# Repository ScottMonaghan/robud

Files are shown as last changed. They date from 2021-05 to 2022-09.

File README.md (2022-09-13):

# Ro-Bud - Lovable, Accessible, Autonomous Companion
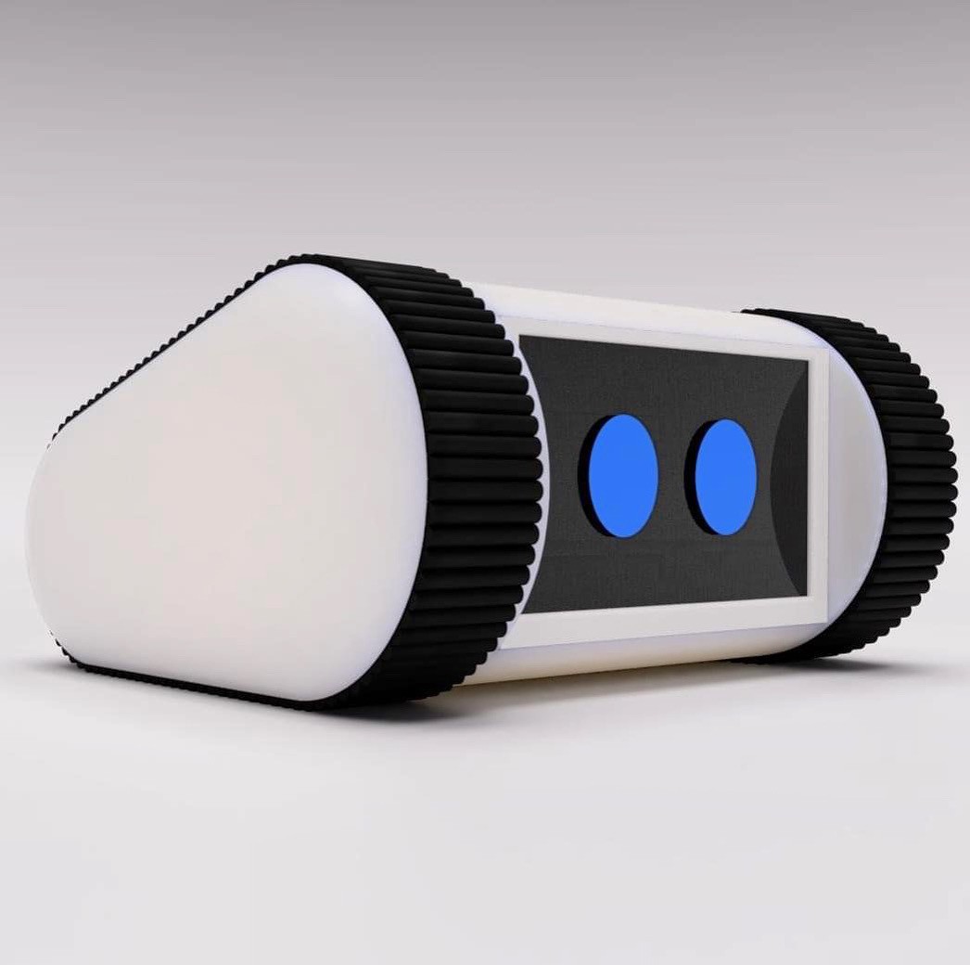
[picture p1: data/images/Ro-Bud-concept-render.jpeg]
Ro-bud
  

## Table of Contents
 * [Summary](#summary)
 * [Description](#description)
 * [Pre-Alpha Build Instructions](#pre-alpha-build-instructions)
   * [Parts Reference](#parts-reference)
   * [Head Assembly](#head-assembly)
 * [Original Project Announcement Videos](#original-project-announcement-videos)
   * [Part 1](#part-1)
   * [Part 2](#part-2)
   * [Part 3](#part-3)
   * [Part 4](#part-4)
## Summary
The Ro-Bud project seeks to create a companion bot that is lovable, accessible to all, and autonomous.  

[Return to Table of Contents](#table-of-contents)

## Description
Challenge: Despite decades of fictional depiction through popular culture, as of 2021, robotic companion bots that even come close to those of popular imagination are not available at scale.

While there have been impressive private for-profit attempts at releasing relatively advanced consumer companion bots, specifically Jibo and Anki Vector, these endeavors ultimately proved commercially unviable, forcing the companies to fold, and effectively removing these wonderfully engineered robots from either availability or full operability (as they were dependent on proprietary services provided by their now-defunct companies).

The Ro-Bud project is an attempt to pick up where Jibo and Ankni left off, and fulfil the dream of providing a consumer robot that is:
1. LOVEABLE - Feels just like a family pet
2. ACCESSIBLE - Can be built by anyone following project instructions with readily available parts with a cost at or under $500
3. AUTONOMOUS - Has it's own goals.  

[Return to Table of Contents](#table-of-contents)

# Alpha Build Instructions
**NOTE: The following build instructions are in-progress and not yet complete**  
Last updated 17-August 2022

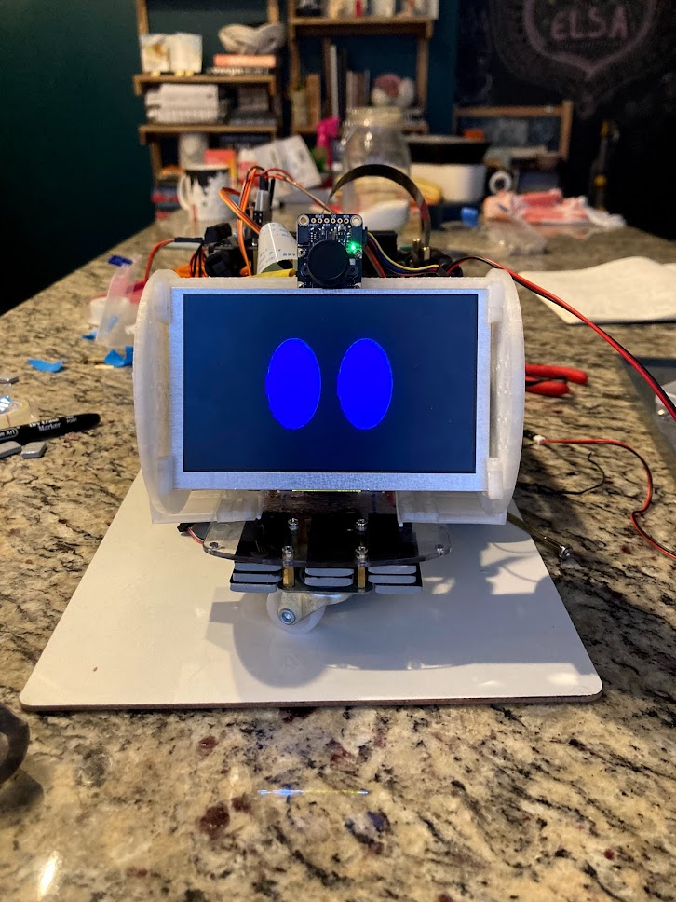
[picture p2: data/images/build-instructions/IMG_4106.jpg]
Pre-Alpha Ro-Bud Build


**Documentation To-Do**
 * [x] Add 3d-printable models
 * [ ] Jetson Wifi Module Install
 * [ ] SD Card Flashing
 * [x] Head Assembly  
 * [ ] Remote VM setup
 * [ ] Remote Operation Instructions

[Return to Table of Contents](#table-of-contents)

## Master Parts Reference
 * A. horizontal braces [stl](./data/stl/robud-horizontal-brace.stl)
 * B. 3-hole fastener [stl](./data/stl/robud-3-hole-fastener.stl)
 * C. 2x8mm round-head self-tapping screws https://www.amazon.com/gp/product/B07NT5288W  
 * D. 2x8mm pan-head-with-washer self-tapping screws https://www.amazon.com/gp/product/B07NTGRFBF  
 * E. BNO055 orientation sensor https://www.adafruit.com/product/4646, https://www.digikey.com/en/products/detail/adafruit-industries-llc/4646/12609996
 * F. SainSmart IMX219 Camera Module https://www.amazon.com/gp/product/B07VFFRX4C  
 * G. VL53L0X time-of-flight distance sensor https://www.adafruit.com/product/3317  
 * H. 1-hole 2mm screw fastener [stl](./data/stl/robud-1-hole-fastener.stl)
 * I. 300mm 15-pin camera ribbon cable https://www.adafruit.com/product/1648
 * J. 100mm Stemma QT JST SH 4-pin cable https://www.adafruit.com/product/4210
 * K. display fastener [stl](./data/stl/robud-display-fastener.stl)
 * L. servo adapter [stl](./data/stl/robud-servo-adapter.stl)
 * M. head barrel wall [stl](./data/stl/robud-head-barrel-wall.stl)
 * N. head shaft adapter [stl](./data/stl/robud-head-shaft-adapter.stl)
 * O. bearing https://www.amazon.com/gp/product/B07S1B3MS6  
 * Q. MG90S 9G micro servo https://www.amazon.com/gp/product/B07F7VJQL5  
 * R. ~~5in display https://www.adafruit.com/product/1678, https://www.digikey.com/en/products/detail/adafruit-industries-llc/1678/10670051
 * S. ~~40 Pin Flexible Flat Ribbon Cable 0.5mm Pitch - 200mm https://www.amazon.com/gp/product/B07C4P6S43
 * T. mono enclosed speaker - 3W 4 Ohm https://www.adafruit.com/product/3351  
 * U. head L bracket [stl](./data/stl/robud-head-L-bracket.stl)
 * V. servo horn (included with servo(Q))
 * W. servo screw (included with servo(Q))
 * CC. SparkFun Qwiic SHIM for Raspberry Pi https://www.sparkfun.com/products/15794
 * DD. Stacking Header for Pi A+/B+/Pi 2/Pi 3 - 2x20 Extra Tall Header https://www.adafruit.com/product/1979
 * EE. Adafruit DC & Stepper Motor Bonnet for Raspberry Pi https://www.adafruit.com/product/4280
 * FF. Break-away 0.1" male header https://www.adafruit.com/product/392
 * GG. Male/Male Jumper Wires - 20 x 6" (150mm) https://www.adafruit.com/product/1957
 * HH. Female/Female Jumper Wires - 20 x 6" (150mm)Female/Female Jumper Wires - 20 x 6" (150mm)
 * II. Heat shrink tubing https://www.adafruit.com/product/1649
 * JJ. 3.5mm (1/8") Stereo Audio Plug Terminal Block https://www.adafruit.com/product/2790
 * KK. Rocker toggle switch (comes with chassis kit)
 * LL. Servo Tester https://www.amazon.com/gp/product/B07TQSKLBK
 * MM. PCA9685 16 Channel 12 Bit PWM Servo Driver https://www.amazon.com/gp/product/B07RMTN4NZ
 * NN. Baseus Power Bank, 65W 20000mAh Laptop Portable Charger https://www.amazon.com/gp/product/B08THCNNCS
 * OO. x2 USB-A Male Plug to 5-pin Terminal Block https://www.amazon.com/gp/product/B07H53X194 (2-pack), https://www.digikey.com/en/products/detail/adafruit-industries-llc/3628/7931507 (1-pack)
 * PP. x2 Stacking Header for Pi https://www.adafruit.com/product/1979, https://www.digikey.com/en/products/detail/adafruit-industries-llc/1979/6238003, https://www.amazon.com/gp/product/B071XCHZNB/(4 pack)
 * QQ. M2.5 brass stand-off kit https://www.amazon.com/gp/product/B075K3QBMX/ (or equivalent)
 * RR. 22AWG Silicone Hook Up Wire (stranded) https://www.amazon.com/gp/product/B07T4SYVYG/ (or equivalent, you want not-too-stiff wire than can handle 4 amps)
 * SS. STEMMA QT / Qwiic JST SH 4-Pin Cable - 400mm long https://www.adafruit.com/product/5385, https://www.digikey.com/en/products/detail/adafruit-industries-llc/5385/16546436
 * TT. Heat Shrink Tubing https://www.amazon.com/gp/product/B01MFA3OFA (can be subbed with electrical tape, or equivalent)
 * UU. 5.0" 40-pin 800x480 TFT Display without Touchscreen https://www.adafruit.com/product/1680
 * VV. TFP401 HDMI/DVI Decoder to 40-Pin TTL Breakout - Without Touch https://www.adafruit.com/product/2218
 * WW. 40-pin FPC Extension Board + 200mm Cable https://www.adafruit.com/product/2098

[Return to Table of Contents](#table-of-contents)
 
## Head Assembly
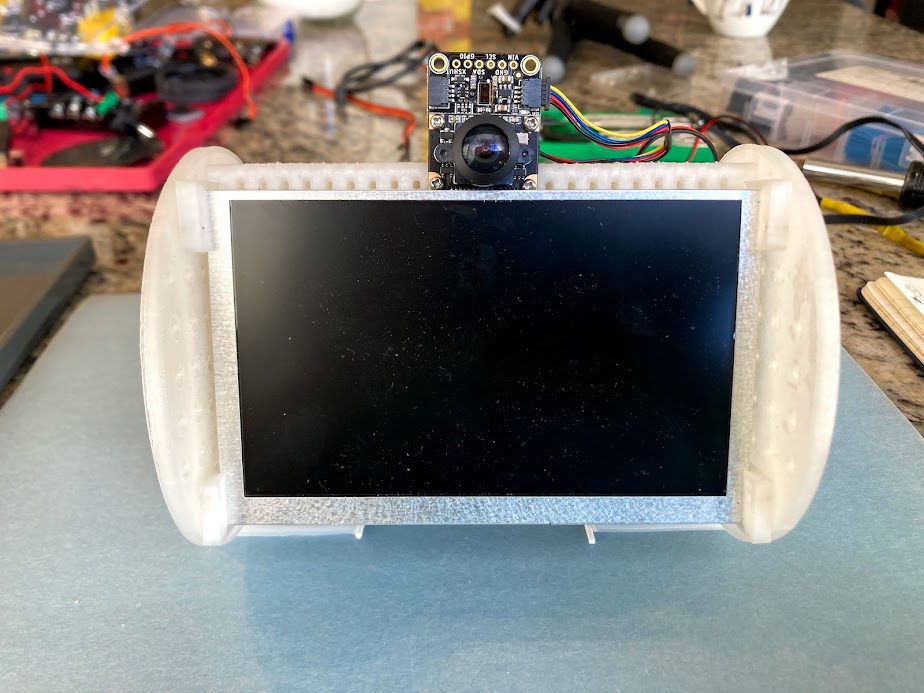
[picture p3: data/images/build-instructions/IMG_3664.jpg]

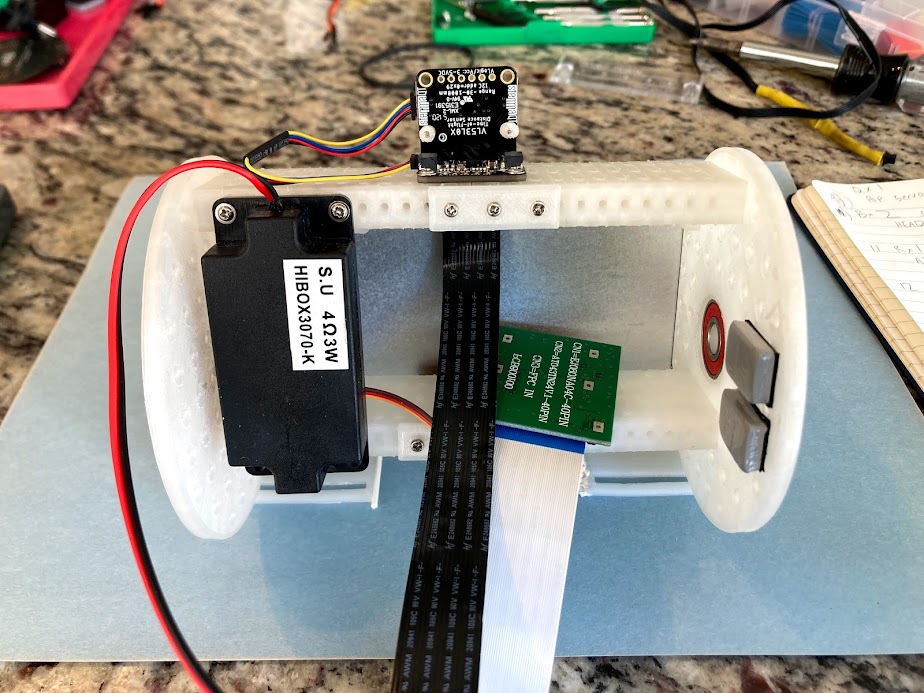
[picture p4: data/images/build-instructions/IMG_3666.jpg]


**Full list of Head Assembly Parts**
   * 3d Printed Parts (Ender 3 settings - PLA, Raft recommended, defaults otherwise) 
     * x4 A. horizontal braces [stl](./data/stl/robud-horizontal-brace.stl)
     * x3 B. 3-hole fastener  [stl](./data/stl/robud-3-hole-fastener.stl)
     * x2 H. 1-hole 2mm screw fastener [stl](./data/stl/robud-1-hole-fastener.stl)
     * x4 K. display fastener [stl](./data/stl/robud-display-fastener.stl)
     * x1 L. servo adapter [stl](./data/stl/robud-servo-adapter.stl)
     * x2 M. head barrel wall [stl](./data/stl/robud-head-barrel-wall.stl)
     * x1 N. head shaft adapter [stl](./data/stl/robud-head-shaft-adapter.stl)
     * x2 U. head L bracket [stl](./data/stl/robud-head-L-bracket.stl)

   * Adafruit (recommend sourcing from DigiKey for best US price/shipping)
     * x1 E. BNO055 orientation sensor https://www.adafruit.com/product/4646, https://www.digikey.com/en/products/detail/adafruit-industries-llc/4646/12609996 (often out of stock due to chip shortage. Check DigiKey, Adafruit, Mouser & Amazon)
     * x1 G. VL53L0X time-of-flight distance sensor https://www.adafruit.com/product/3317, https://www.digikey.com/en/products/detail/adafruit-industries-llc/3317/6569762
     * x1 I. 300mm 15-pin camera ribbon cable https://www.adafruit.com/product/1648, https://www.digikey.com/en/products/detail/adafruit-industries-llc/1648/7035020
     * x1 J. 100mm Stemma QT JST SH 4-pin cable https://www.adafruit.com/product/4210, https://www.digikey.com/en/products/detail/adafruit-industries-llc/4210/10230021
     * ~~x1 R. 5in display https://www.adafruit.com/product/1678
     * x1 T. mono enclosed speaker - 3W 4 Ohm https://www.adafruit.com/product/3351  

   * Amazon
     * x7 C. 2x8mm round-head self-tapping screws https://www.amazon.com/gp/product/B07NT5288W  
     * x20 D. 2x8mm pan-head-with-washer self-tapping screws https://www.amazon.com/gp/product/B07NTGRFBF 
     * x1 F. SainSmart IMX219 Camera Module https://www.amazon.com/gp/product/B07VFFRX4C  
     * x1 O. bearing https://www.amazon.com/gp/product/B07S1B3MS6 
     * x1 Q. MG90S 9G micro servo https://www.amazon.com/gp/product/B07F7VJQL5
     * x1 ~~S. 40 Pin Flexible Flat Ribbon Cable 0.5mm Pitch - 200mm https://www.amazon.com/gp/product/B07C4P6S43
     * x1 V. servo horn (packaged with Q MG90S 9G micro servo)
     * x1 W. server screw (packaged with Q MG90S 9G micro servo)
     * x1 LL. Servo Tester https://www.amazon.com/gp/product/B07TQSKLBK
     * x1 MM. PCA9685 16 Channel 12 Bit PWM Servo Driver https://www.amazon.com/gp/product/B07RMTN4NZ
     * x1 UU. 5.0" 40-pin 800x480 TFT Display without Touchscreen https://www.adafruit.com/product/1680
     * x1 VV. TFP401 HDMI/DVI Decoder to 40-Pin TTL Breakout - Without Touch https://www.adafruit.com/product/2218
     * x1 WW. 40-pin FPC Extension Board + 200mm Cable https://www.adafruit.com/product/2098
   
### 1. Attach two horizontal braces(A) with 3-hole fastener(B) & attach BNO-055  orientation sensor(E)  

**Parts:**  
   * x2 A. horizontal braces  
   * x1 B. 3-hole fastener  
   * x3 C. 2x8mm round-head self-tapping screws  
   * x4 D. 2x8mm pan-head-with-washer self-tapping screws  
   * x1 E. BNO055 orientation sensor

>_**Notes:**_ 
>   * _Make sure Y axis of BNO055(E) points toward picture as shown in image_
>   * _Only fasten one side of the horizontal braces(E)_
     
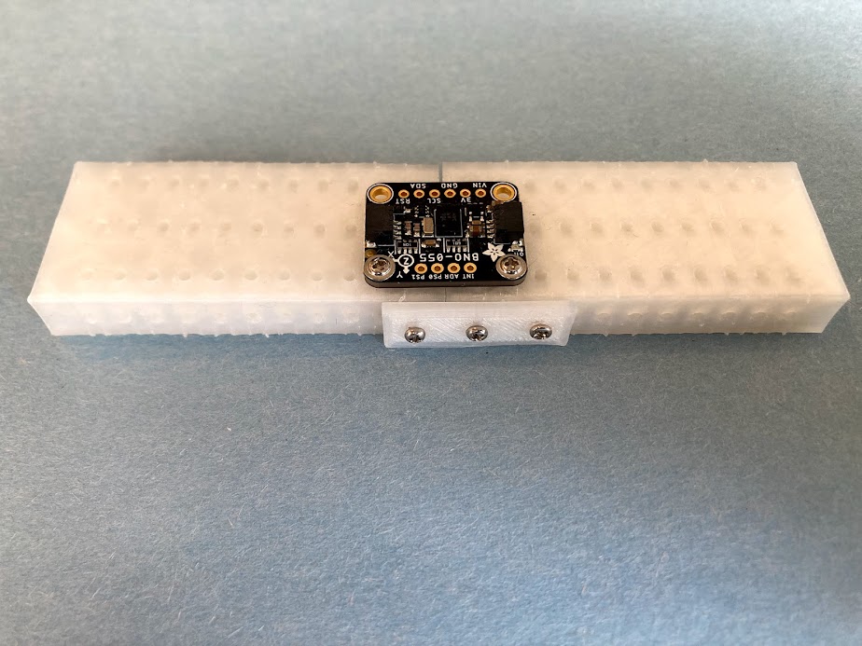
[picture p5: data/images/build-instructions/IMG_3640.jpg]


---
### 2. Turn 180 degrees and attach camera(F) 

**Parts:**  
   * x1 F. SainSmart IMX219 Camera Module
   * x2 C. 2x8mm round-head self-tapping screws

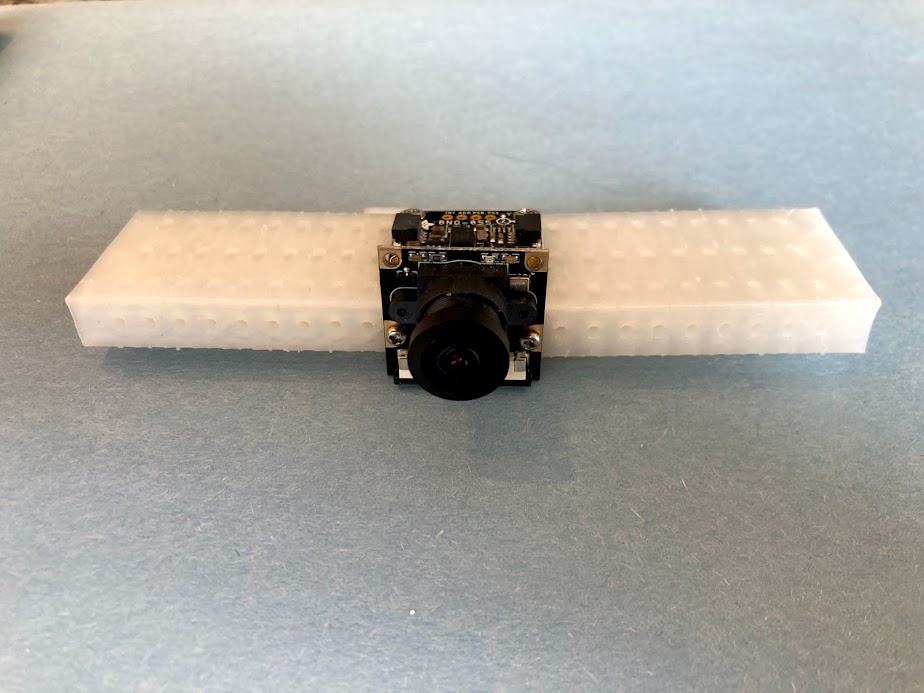
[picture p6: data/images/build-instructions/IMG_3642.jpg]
Head Assembly Step 2


---    
### 3. Attach VL53L0X time-of-flight distance sensor(G) 

**Parts:** 
  * x2 H. 1-hole 2mm screw fastener  
  * x2 C. 2x8mm round-head self-tapping screws  
  * x1 G. VL53L0X time-of-flight distance sensor  
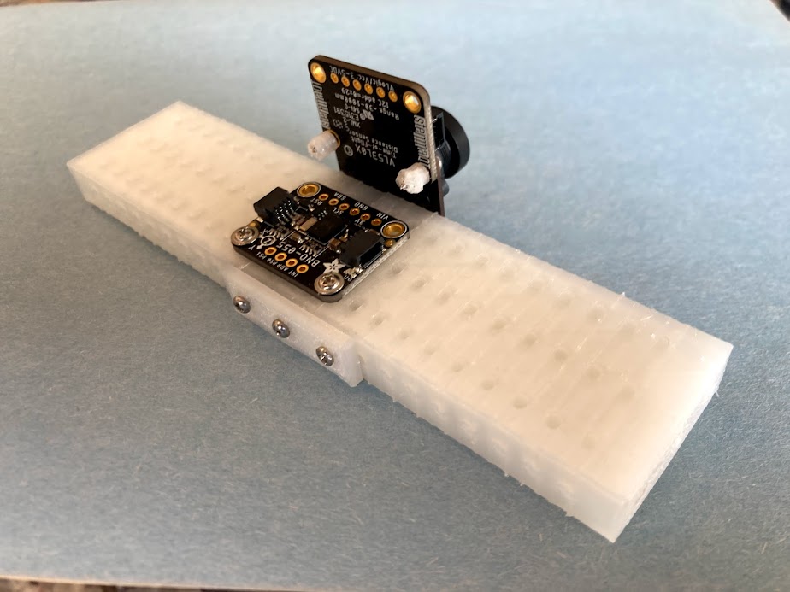
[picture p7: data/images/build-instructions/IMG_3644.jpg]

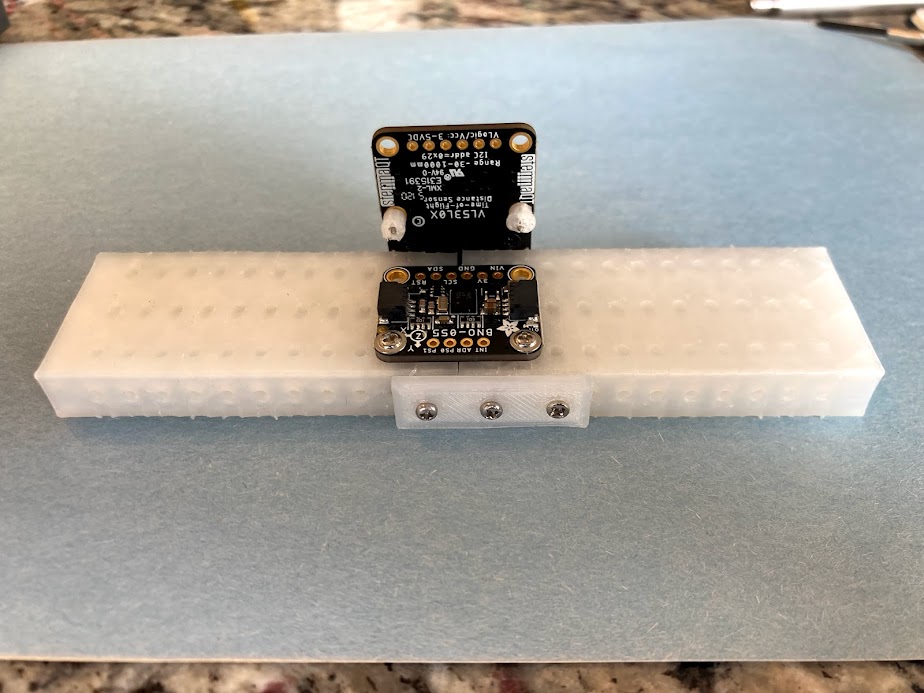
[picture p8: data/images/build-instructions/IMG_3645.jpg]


---     
### 4. Attach camera 15-pin ribbon(I) cable & STEMMA QT cable(J)

**Parts:** 
  * x1 I. 300mm 15-pin camera ribbon cable
  * x1 J. 100mm Stemma QT JST SH 4-pin cable

>_**Notes:**_ 
>   * _Make sure pins of ribbon cable are facing toward contacts and fastened securely_
>   * _Attatch STEMMA QT cable(J) securely to right STEMMA sockets on VL53L0X(G) and BNO055(E)_
   
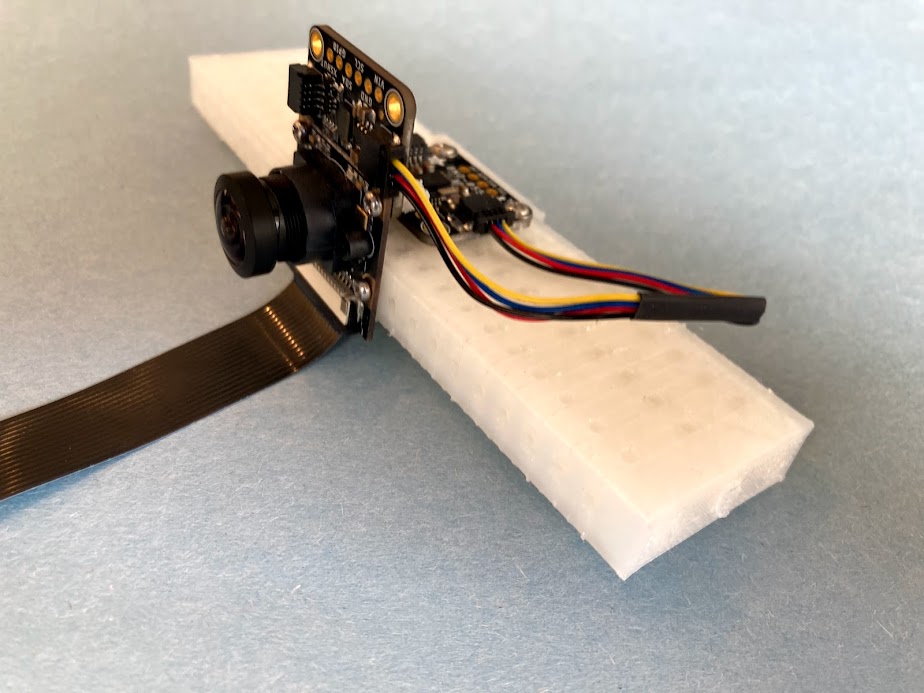
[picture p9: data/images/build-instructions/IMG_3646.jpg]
Head Assembly Step 4


---   
### 5. Attach display fasteners(K) and servo adapter(L) to left barrel wall(M)
**Parts:**  
 * x1 M. head barrel wall
 * x1 L. servo adapter
 * x2 K. display fastener
 * x4 D. 2x8mm pan-head-with-washer self-tapping screws

>_**Notes:**_
>   * _Make sure fasteners and raised center lip are on opposite sides_
>   * _Make sure slotted sides of the display fasteners(K) are face up, with open sides pointed inside the circle, and closed ends are pointed out_
>   * _Make sure servo adapter is oriented as shown in image_
>   * _If servo adapter cannot be popped in, soften with a hair dryer or heat gun_
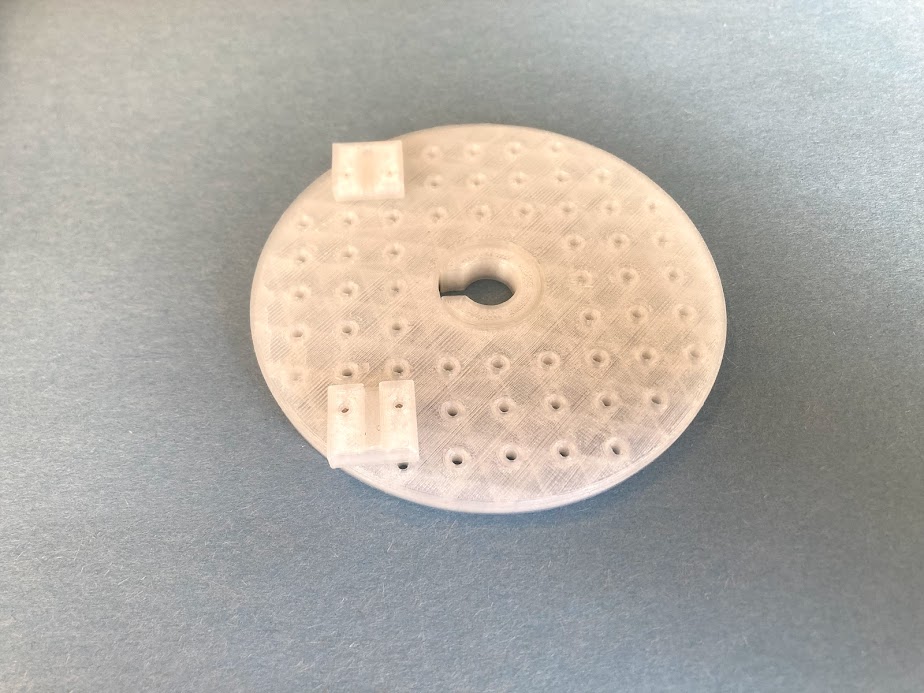
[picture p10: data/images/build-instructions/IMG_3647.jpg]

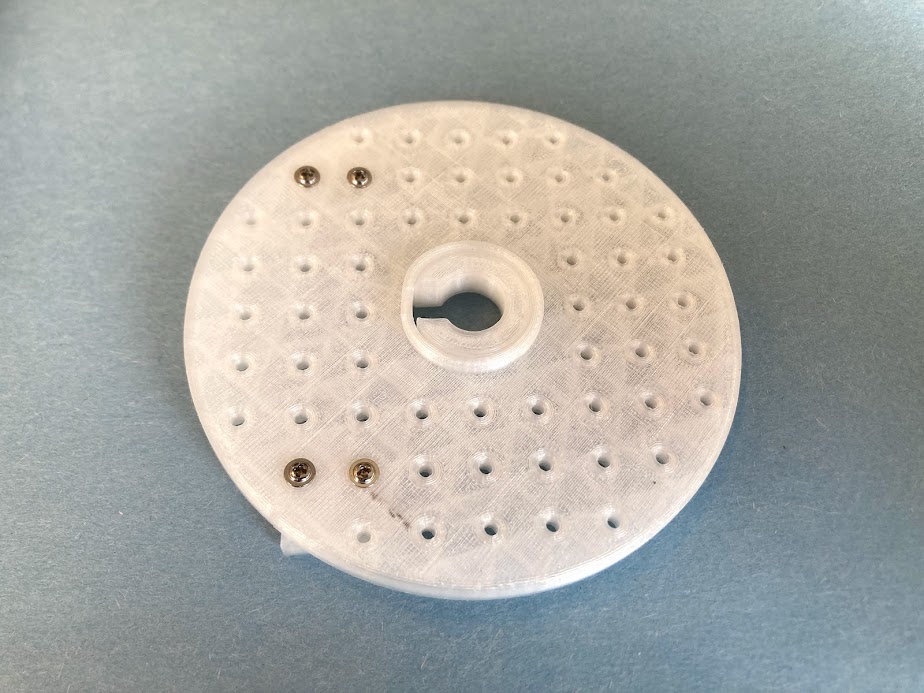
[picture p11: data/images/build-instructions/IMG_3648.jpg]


---   
### 6. Use the servo tester to set servo to neutral position (90 degrees)
**Parts:**  
   * x1 Q. MG90S 9G micro servo
   * x1 LL. Servo Tester
---   
### 7. Pop servo(Q) into left barrel wall(M)
**Parts:**  
   * x1 Q. MG90S 9G micro servo  
   * x2 M. left barrel wall(M) from step 5  

>_**Notes:**_
>   * _Body of servo should be on same side as fasteners from step 5_  
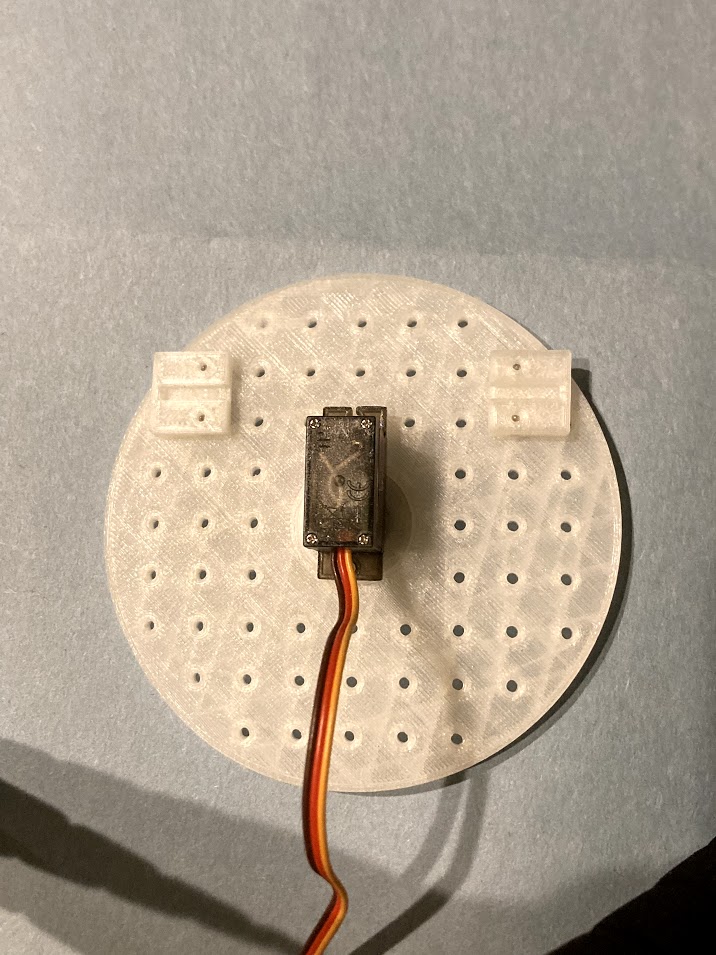
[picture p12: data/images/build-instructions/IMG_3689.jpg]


---   
### 8. Add shaft(N) to bearing(O)
**Parts:**  
 * x1 N. head shaft adapter 
 * x1 O. bearing 

>_**Notes:**_
>   * _If shaft cannot be popped in, soften with a hair dryer or heat gun_
>   * _The longer side of the shaft should be in the bearing_
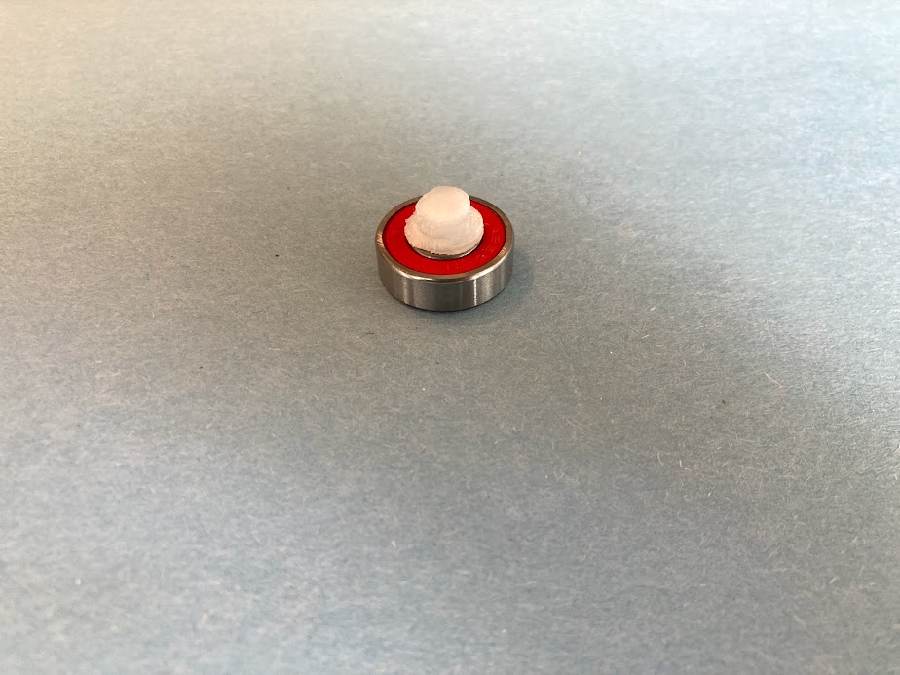
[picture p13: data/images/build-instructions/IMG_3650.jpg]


---   
### 9. Attach display fasteners(K) to right barrel wall(M)
**Parts:**  
 * x1 M. head barrel wall
 * x2 K. display fastener

>_**Notes:**_
>  * _Make sure fasteners and raised center lip are on opposite sides_
>  *_Balance weights shown in photo are no-longer used. Please ignore_
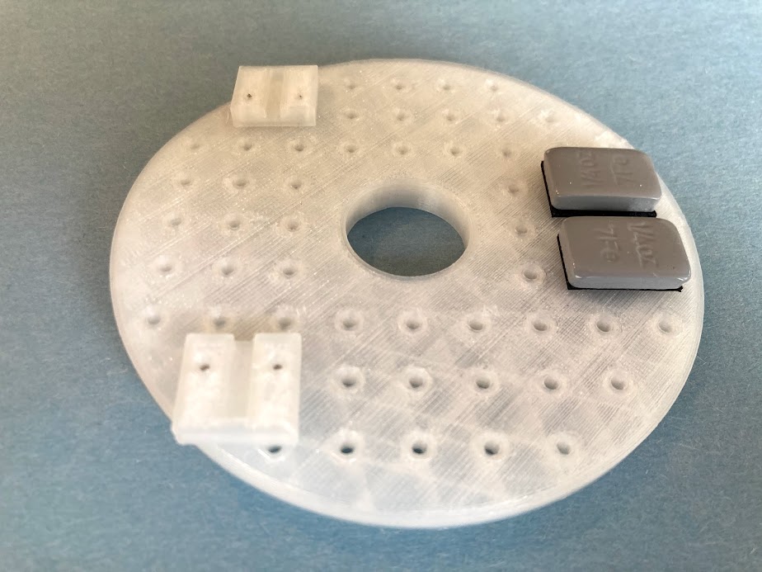
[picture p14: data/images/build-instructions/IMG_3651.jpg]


---   
### 10. Pop bearing(O) into right barrel wall(M)
**Parts:**  
 * x1 bearing(O) with shaft(N) from step 8
 * x1 right barrel wall(M) from step 9

>_**Notes:**_
>   * _Make sure shaft is on the opposite side of the clips & weights_
>   * _If bearing cannot be popped in, soften with a hair dryer or heat gun_
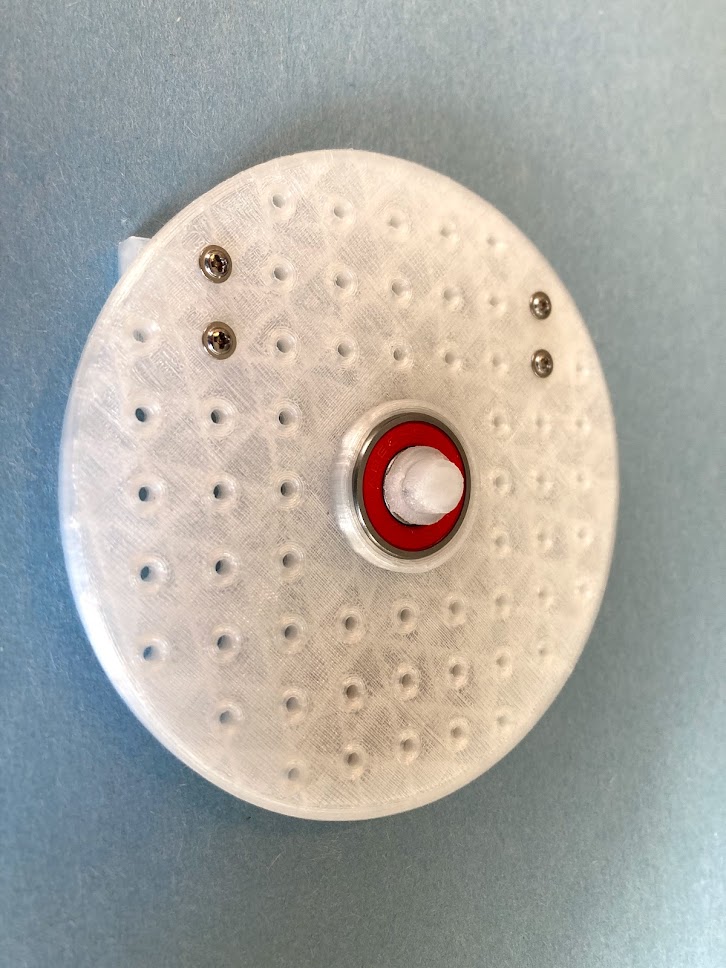
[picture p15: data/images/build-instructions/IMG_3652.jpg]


---   
### 11. Attach two horizontal braces(A) with two 3-hole fasteners(B) to create lower head brace
**Parts:**  
   * x2 A. horizontal braces  
   * x2 B. 3-hole fasteners  

>_**Notes:**_
>  * _Make sure to add 3-hole fastener(B) to both sides_
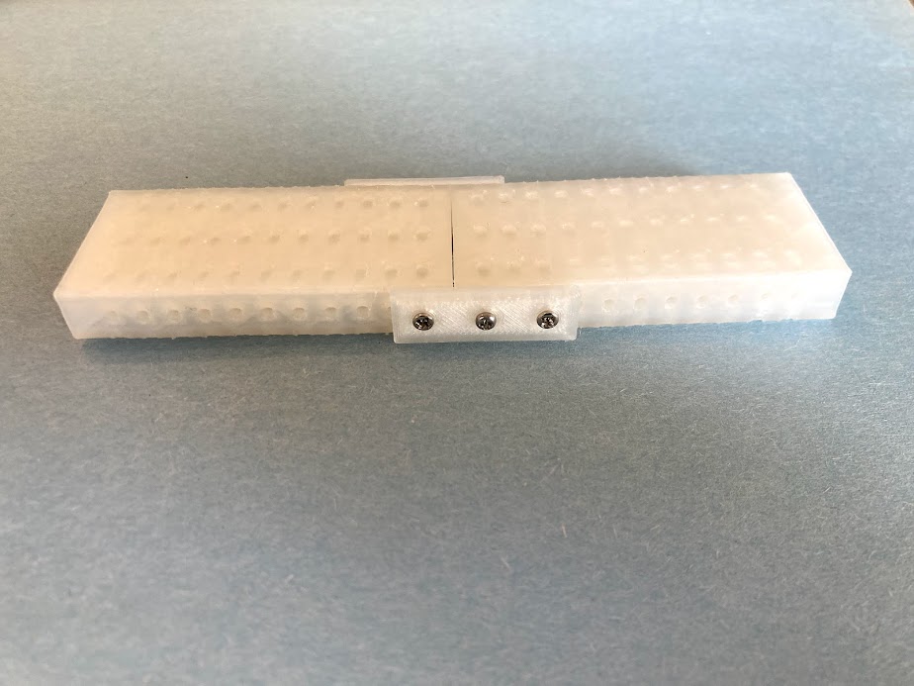
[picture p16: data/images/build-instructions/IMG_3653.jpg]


---   
### 12. Attach bottom head brace to left barrel wall
**Parts:**  
   * x1 Left barrel wall with servo (from step 7)  
   * x1 Lower horizontal head brace (from step 11)  
   * x2 D. 2x8mm pan-head-with-washer self-tapping screws
  
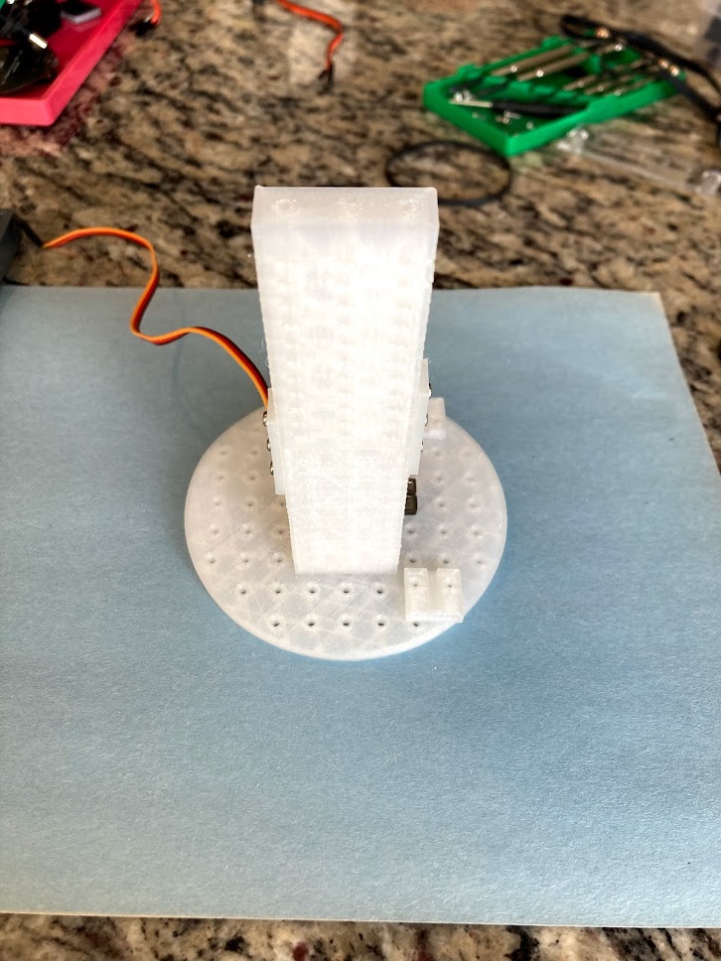
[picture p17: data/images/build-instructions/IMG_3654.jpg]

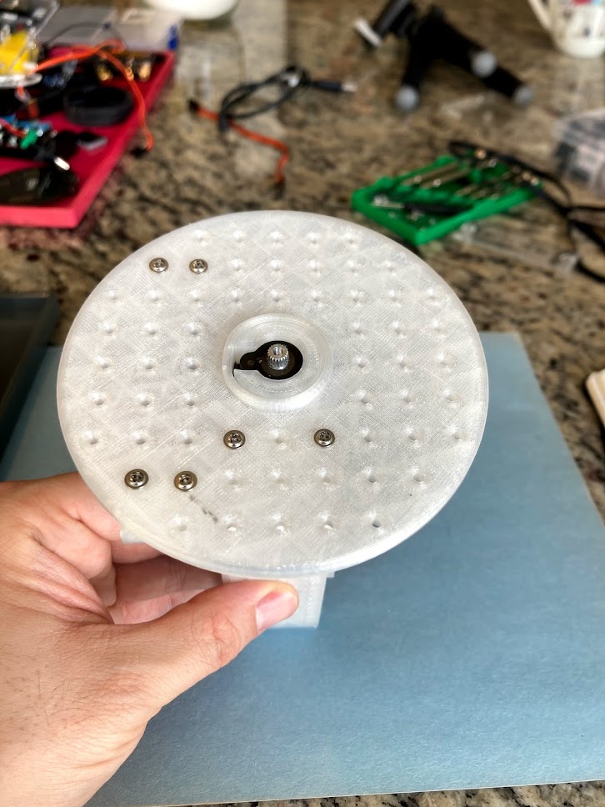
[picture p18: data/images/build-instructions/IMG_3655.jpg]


---   
### 13. Attach top head brace to left barrel wall
**Parts:**  
   * x1 Left barrel wall with servo (from step 12)  
   * x1 Top horizontal head brace with camera (from step 1)  
   * x2 D. 2x8mm pan-head-with-washer self-tapping screws
  
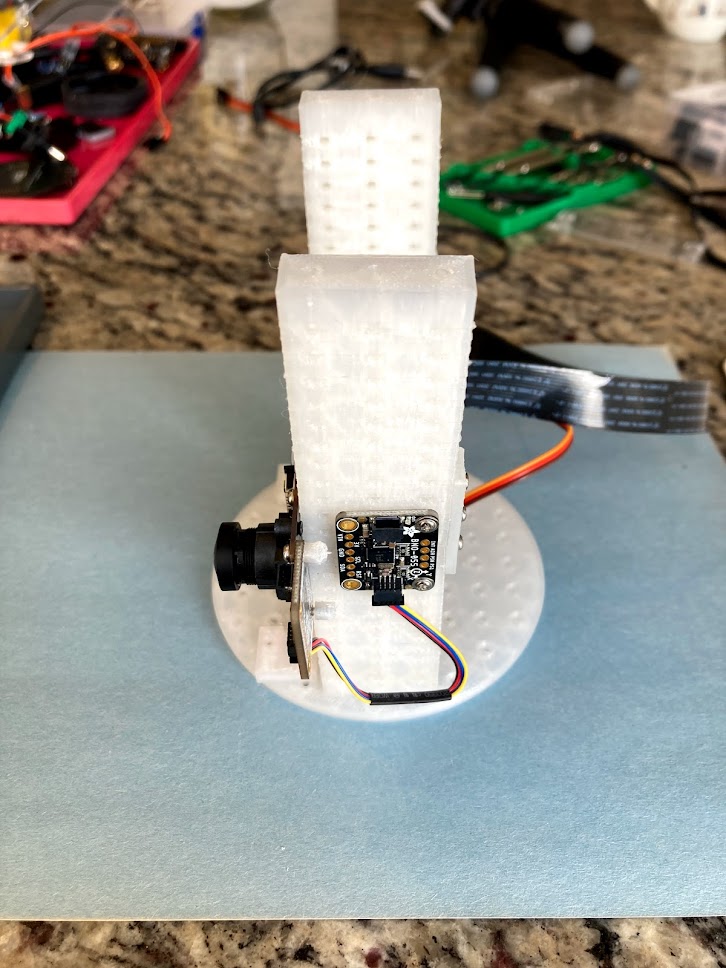
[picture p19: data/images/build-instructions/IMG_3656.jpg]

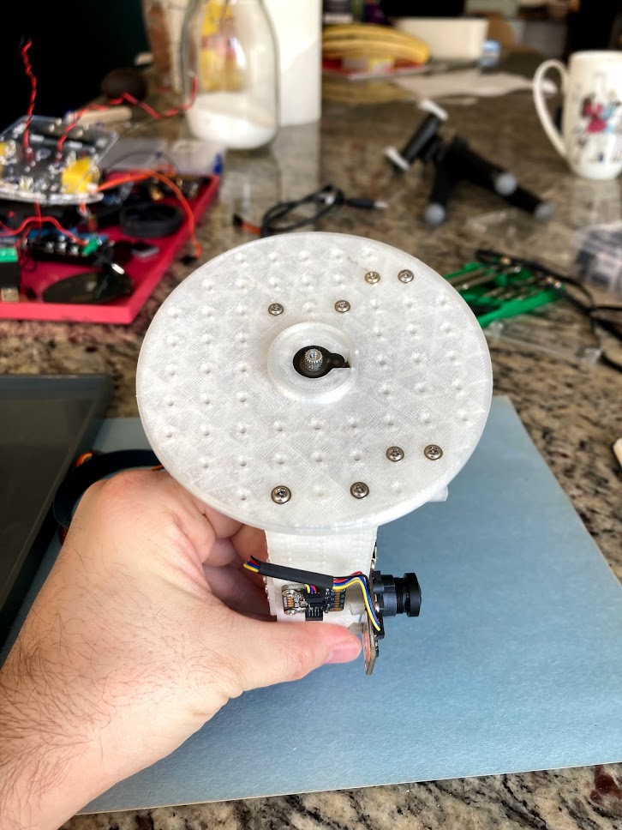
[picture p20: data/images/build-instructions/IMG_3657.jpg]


---   
### 14. Attach 40-pin display ribbon(S) to display(R)  
**Parts:**  
   * x1 R. 7in display  
   * x1 S. 250mm 40pin display ribbon cable  

>_**Notes:**_
>   * _Make sure pins of ribbon cable are facing toward contacts and fastened securely_
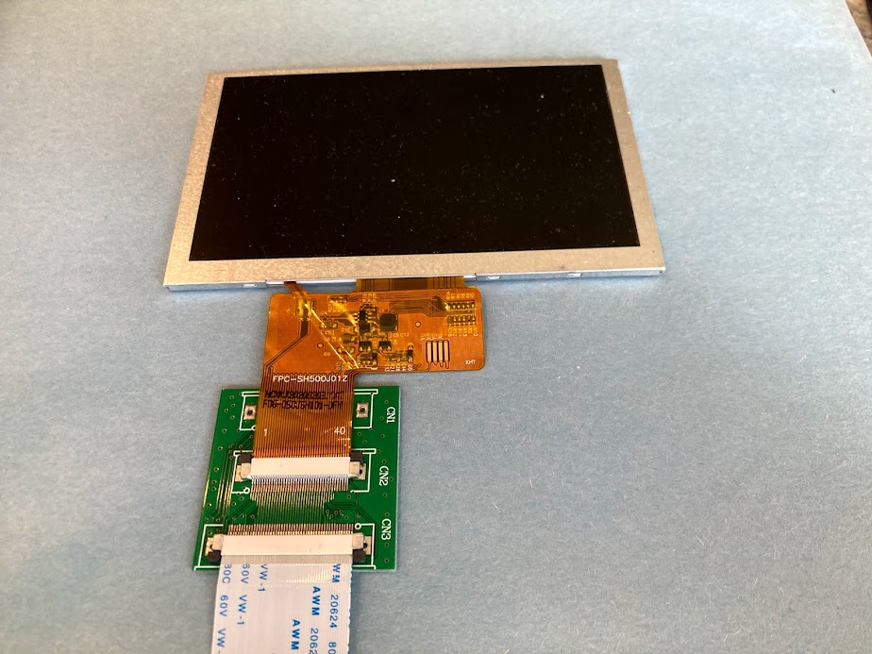
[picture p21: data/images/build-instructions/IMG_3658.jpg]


---   
### 15. Pop display(S) into clips of left barrel wall(M)
**Parts:**  
   * x1 R. 7in display  
   * x1 left barrel wall with servo (from step 12)  

>_**Notes:**_
>   * _Make sure the cables are on the bottom (opposite camera) and feed bewtween both horizontal braces_

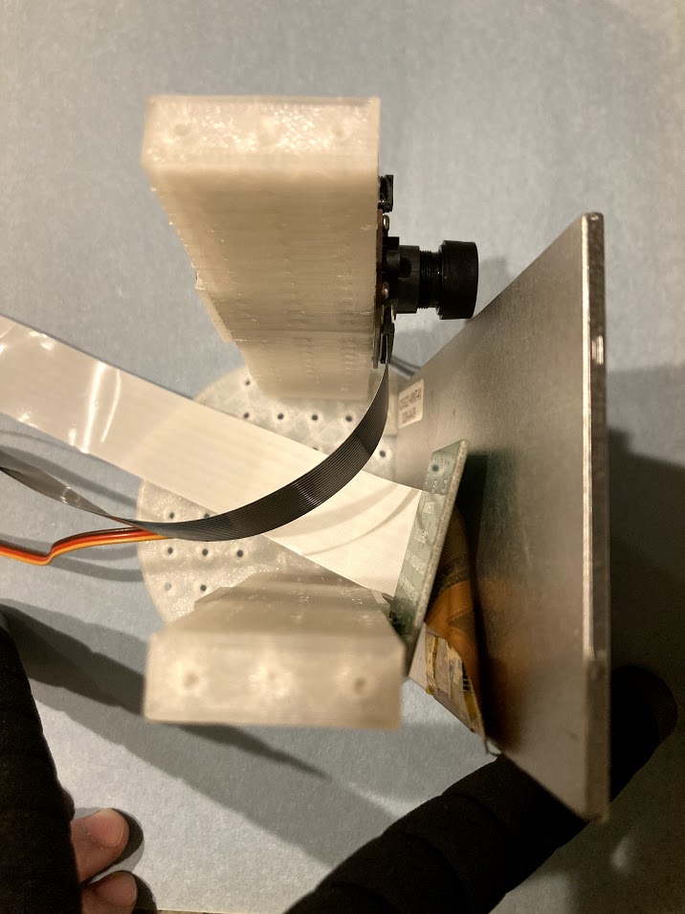
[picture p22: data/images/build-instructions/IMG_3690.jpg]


---   
### 16. Pop right barrel(M) display fasteners(K) onto display and secure to horizontal braces(A) 
**Parts:**  
   * x1 right barrel wall(M) with bearing and shaft (from step 10)
   * x2 D. 2x8mm pan-head-with-washer self-tapping screws

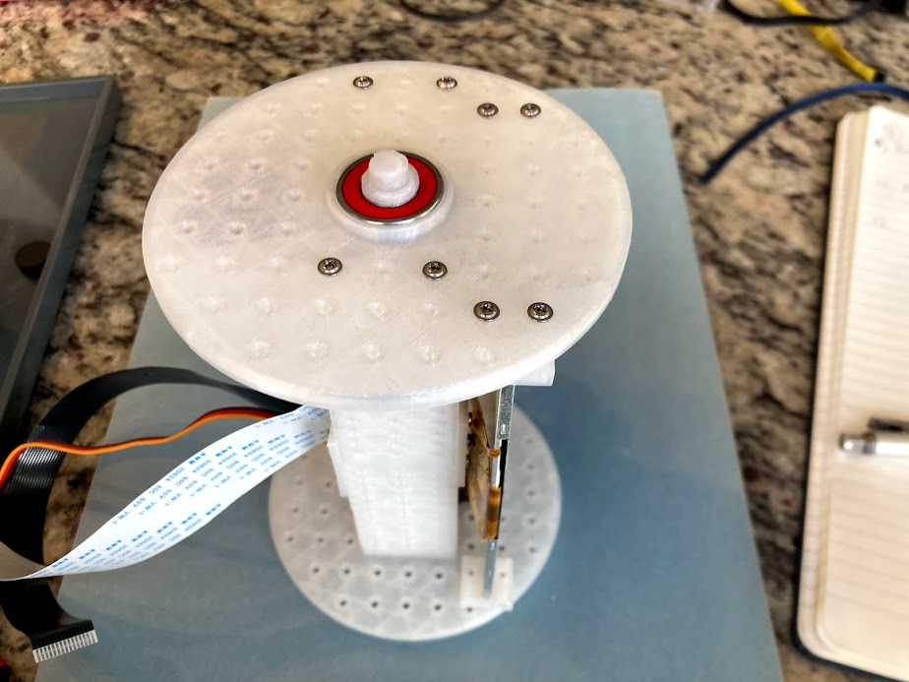
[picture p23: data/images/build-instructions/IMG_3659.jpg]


---   
### 17. Attach speaker(T)
**Parts:**  
   * x1 T. mono enclosed speaker - 3W 4 ohm
   * x2 D. 2x8mm pan-head-with-washer self-tapping screws

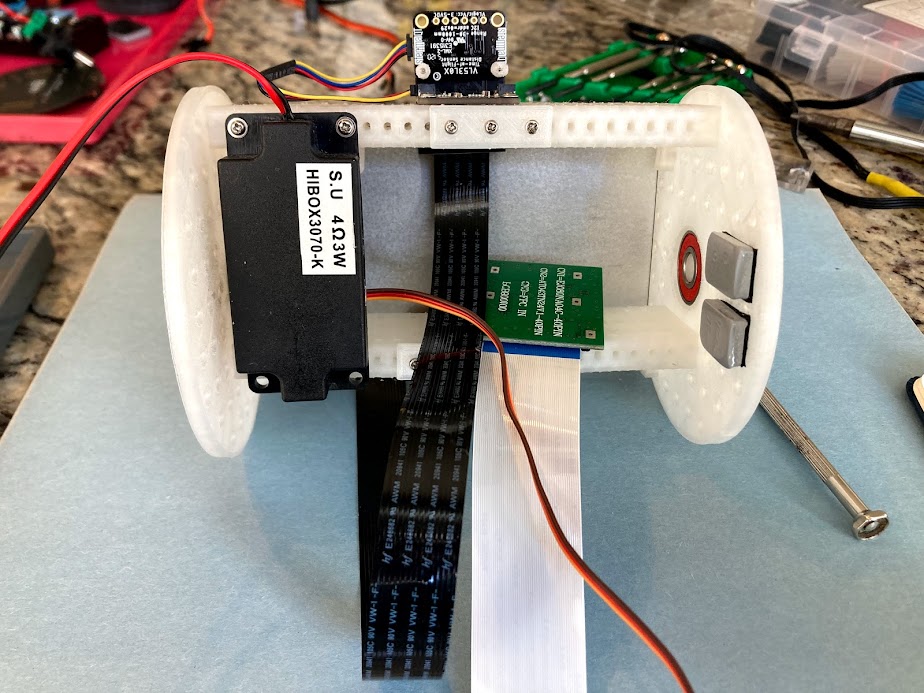
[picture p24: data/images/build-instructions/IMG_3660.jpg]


---   
### 18. Pop right L bracket(U) on bearing shaft
**Parts:**  
   * x1 U. head L bracket

>_**Notes:**_
>   * _If shaft does not pop onto L bracket, use hair dryer or heat gun to soften_

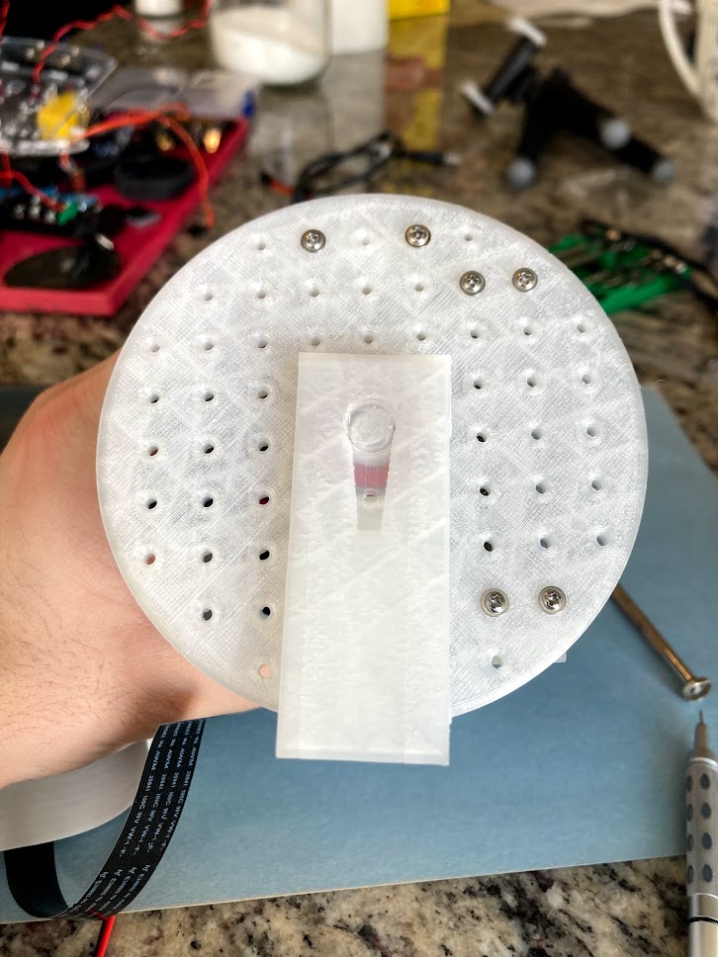
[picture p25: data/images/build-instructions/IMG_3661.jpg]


---   
### 19. Attatch servo horn to remaining L bracket(L) and secure with screw(D)
**Parts:**  
   * x1 U. head L bracket
   * x1 V. servo horn
   * x1 D. 2x8mm pan-head-with-washer self-tapping screw

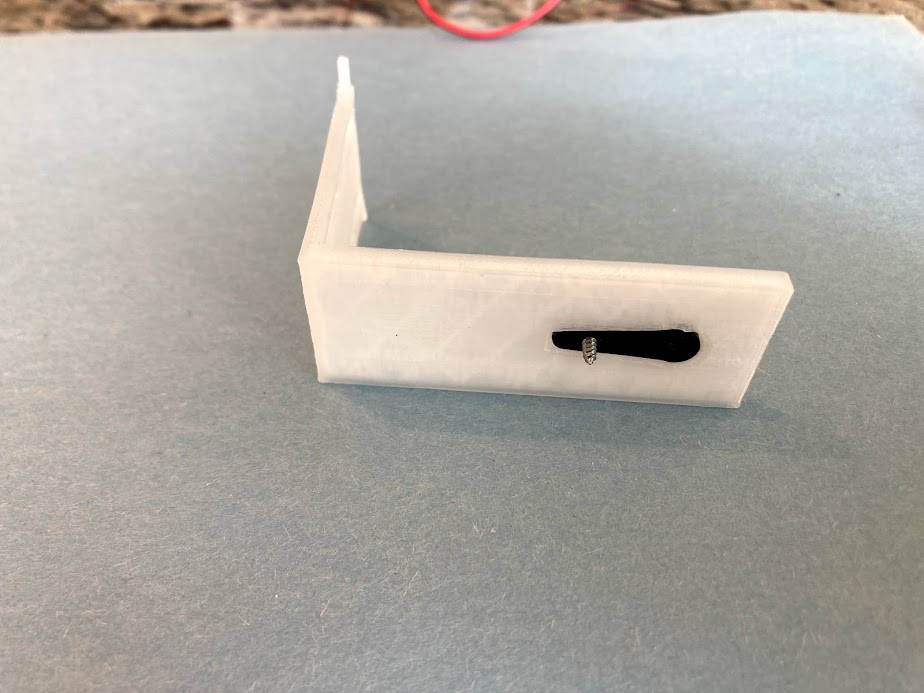
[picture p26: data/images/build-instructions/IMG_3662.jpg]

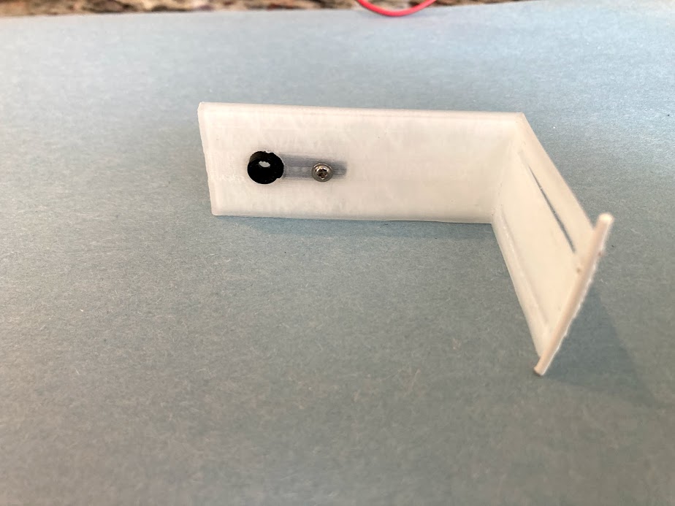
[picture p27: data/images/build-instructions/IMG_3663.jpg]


---   
### 20. Secure left L bracket to head with servo screw(W)
**Parts:**  
   * x1 W. server screw

>_**Notes:**_
>  * _IMPORTANT: The servo horn should be pointing straight down attached with screen pointing straight left_
>  * _Be careful not to turn servo shaft when attaching. If you do, repeat step 6._

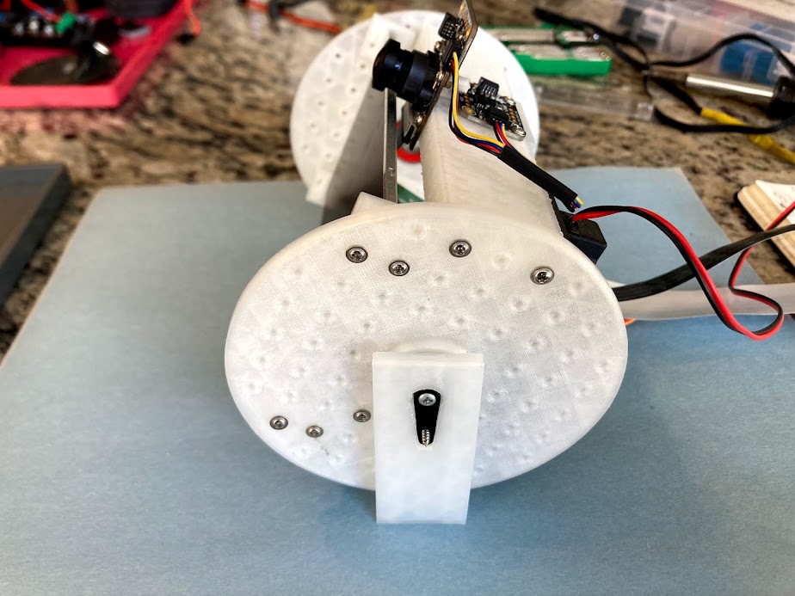
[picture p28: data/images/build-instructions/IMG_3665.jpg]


---   
### 21. The head is now complete and should match the images below:  

Head Assembly Step 5
Head Assembly Step 5
Head Assembly Step 5
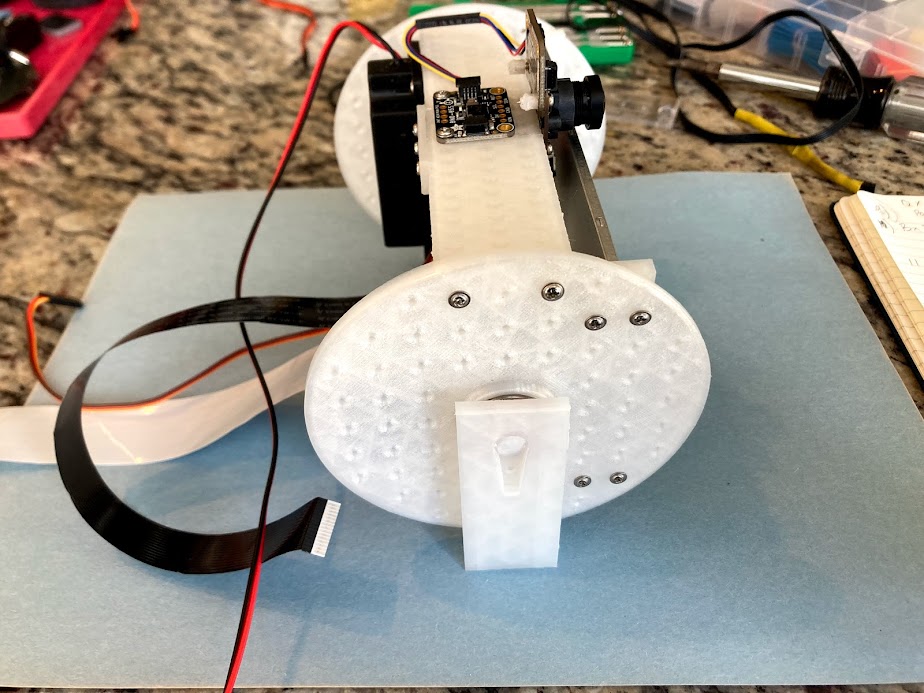
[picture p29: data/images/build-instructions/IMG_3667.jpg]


[Return to Table of Contents](#table-of-contents)

---
## Original Project Announcement Videos  
These videos are the original annoucement and project plan for Ro-Bud uploaded to TikTok on 17-April 2021.  

[Return to Table of Contents](#table-of-contents)
### Part 1  
Ro-Bud Project - Part 1 (https://www.youtube.com/watch?v=bj4LzYycwYc)  

[Return to Table of Contents](#table-of-contents)
### Part 2
Ro-Bud Project - Part 2 (https://www.youtube.com/watch?v=H4fC_qm8pPo)  

[Return to Table of Contents](#table-of-contents)
### Part 3
Ro-Bud Project - Part 3 (https://www.youtube.com/watch?v=r7C16MHGqBg)  

[Return to Table of Contents](#table-of-contents)
### Part 4
Ro-Bud Project - Part 4 (https://www.youtube.com/watch?v=n2G9MuK9-XE)  

[Return to Table of Contents](#table-of-contents)

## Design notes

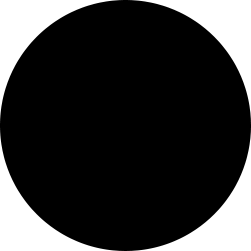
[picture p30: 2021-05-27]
robud_face/Images/robud_round_lid.png

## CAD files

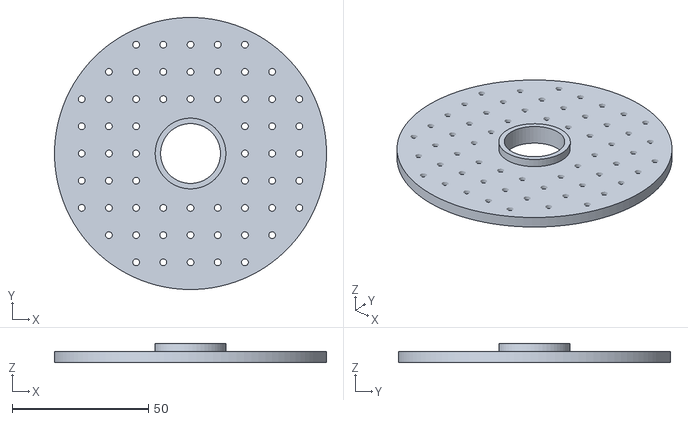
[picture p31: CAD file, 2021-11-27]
data/stl/robud-head-barrel-wall.stl
100.0 x 100.0 x 7.00

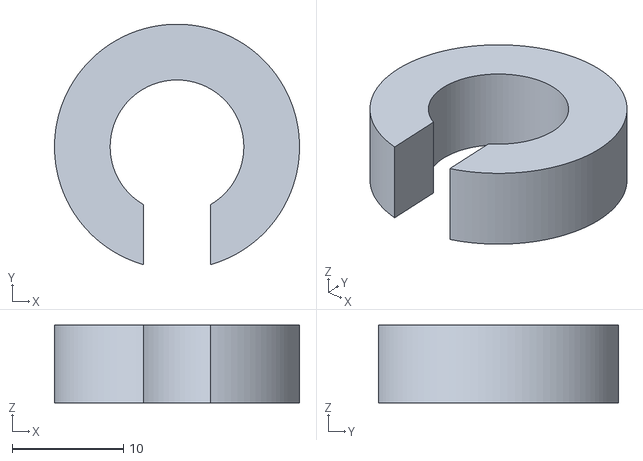
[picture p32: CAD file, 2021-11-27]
data/stl/robud-servo-adapter.stl
22.0 x 21.6 x 7.00

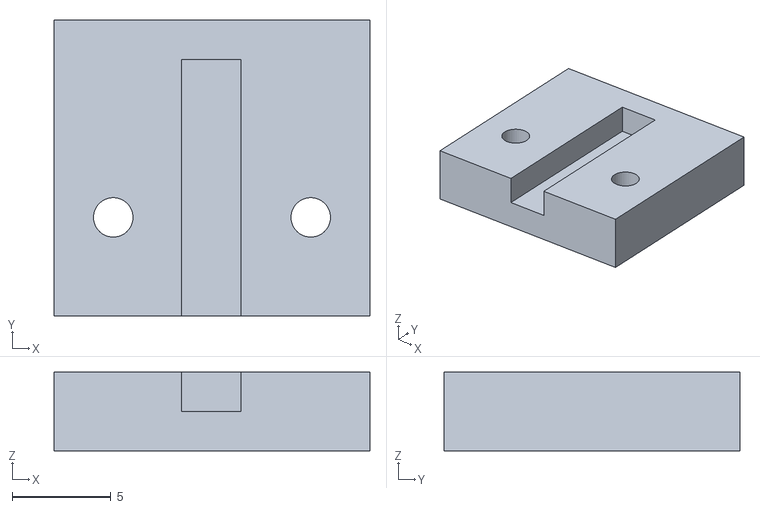
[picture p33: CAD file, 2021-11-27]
data/stl/robud-display-fastener.stl
16.0 x 15.0 x 4.00

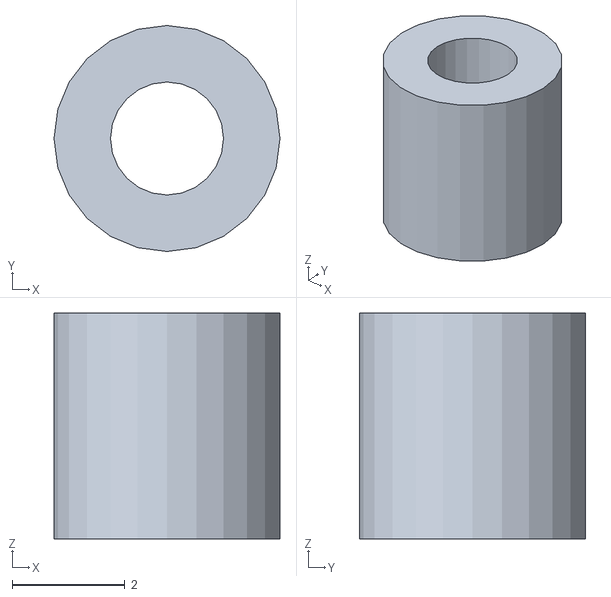
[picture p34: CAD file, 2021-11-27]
data/stl/robud-1-hole-fastener.stl
4.00 x 4.00 x 4.00

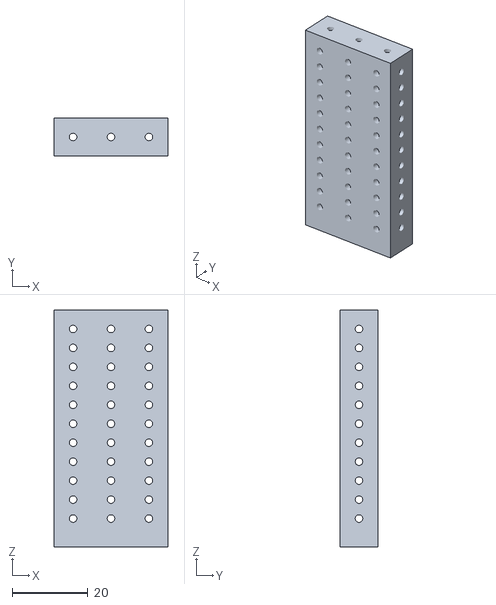
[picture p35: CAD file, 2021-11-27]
data/stl/robud-horizontal-brace.stl
30.0 x 10.0 x 62.5

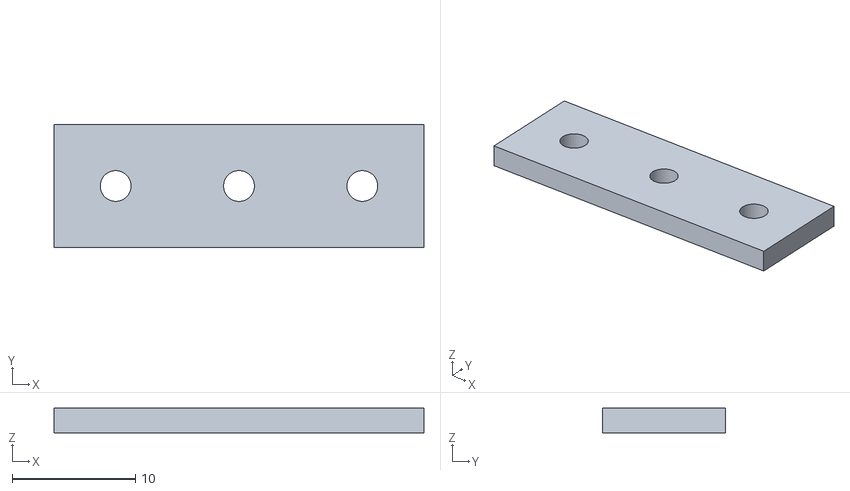
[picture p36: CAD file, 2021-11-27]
data/stl/robud-3-hole-fastener.stl
30.0 x 10.0 x 2.00

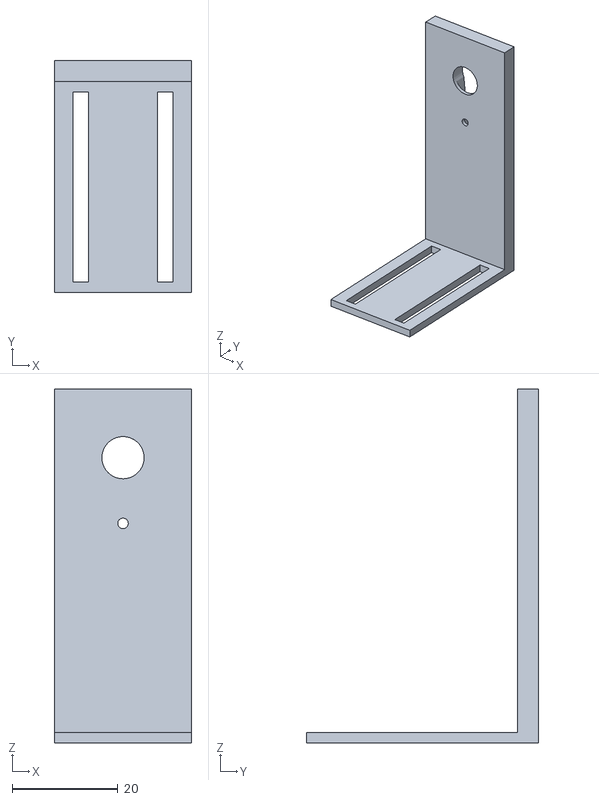
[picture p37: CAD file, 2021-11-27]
data/stl/robud-head-L-bracket.stl
26.0 x 44.0 x 67.0

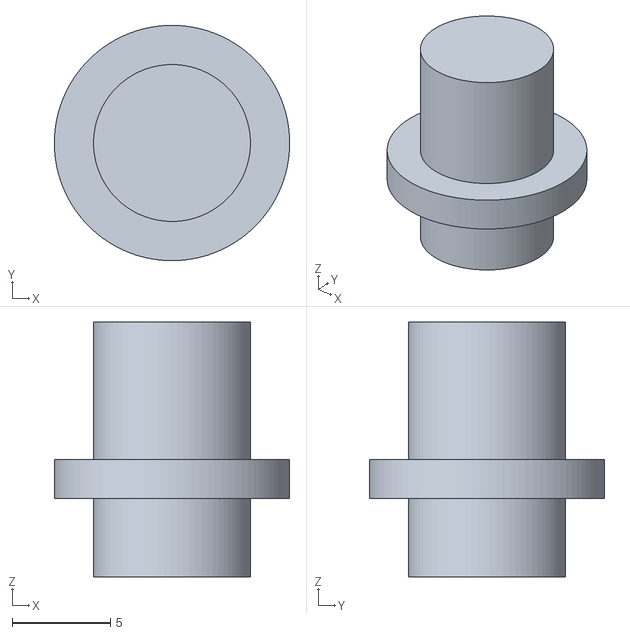
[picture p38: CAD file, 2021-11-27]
data/stl/robud-head-shaft-adapter.stl
12.0 x 12.0 x 13.0

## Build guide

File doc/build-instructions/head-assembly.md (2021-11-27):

## Head Assembly
Head Assembly Step 1
Head Assembly Step 1

### 1. Attach two horizontal braces(A) with 3-hole fastener(B) & attach BNO-055  orientation sensor(E)  

**Parts:**  
   * x2 A. horizontal braces  
   * x1 B. 3-hole fastener  
   * x3 C. 2x8mm round-head self-tapping screws  
   * x4 D. 2x8mm pan-head-with-washer self-tapping screws  
   * x1 E. BNO055 orientation sensor  

>_**Notes:**_ 
>   * _Make sure Y axis of BNO055(E) points toward picture as shown in image_
>   * _Only fasten one side of the horizontal braces(E)_
     
Head Assembly Step 1

---
### 2. Turn 180 degrees and attach camera(F) 

**Parts:**  
   * x1 F. SainSmart IMX219 Camera Module
   * x2 C. 2x8mm round-head self-tapping screws

Head Assembly Step 2

---    
### 3. Attach VL53L0X time-of-flight distance sensor(G) 

**Parts:** 
  * x2 H. 1-hole 2mm screw fastener  
  * x2 C. 2x8mm round-head self-tapping screws  
  * x1 G. VL53L0X time-of-flight distance sensor  
Head Assembly Step 3
Head Assembly Step 3

---     
### 4. Attach camera 15-pin ribbon(I) cable & STEMMA QT cable(J)

**Parts:** 
  * x1 I. 300mm 15-pin camera ribbon cable
  * x1 J. 100mm Stemma QT JST SH 4-pin cable

>_**Notes:**_ 
>   * _Make sure pins of ribbon cable are facing toward contacts and fastened securely_
>   * _Attatch STEMMA QT cable(J) securely to right STEMMA sockets on VL53L0X(G) and BNO055(E)_
   
Head Assembly Step 4

---   
### 5. Attach display fasteners(K) and servo adapter(L) to left barrel wall(M)
**Parts:**  
 * x1 M. head barrel wall
 * x1 L. servo adapter
 * x2 K. display fastener
 * x4 D. 2x8mm pan-head-with-washer self-tapping screws

>_**Notes:**_
>   * _Make sure fasteners and raised center lip are on opposite sides_
>   * _Make sure slotted sides of the display fasteners(K) are face up, with open sides pointed inside the circle, and closed ends are pointed out_
>   * _Make sure servo adapter is oriented as shown in image_
>   * _If servo adapter cannot be popped in, soften with a hair dryer or heat gun_
Head Assembly Step 5
Head Assembly Step 5

---   
### 6. Backdrive servo to 90 degrees
**Parts:**  
   * x1 Q. MG90S 9G micro servo  

>_**Notes:**_
>   * _Suggested steps:_
>     * _Use pliars to gently turn the servo shaft counter-clockwise until you hit the physical stop._
>     * _Then position your pliars at the top at 12:00 as shown in the first picture._
>     * _Finally, carefully turn the shaft clockwise 90 degrees to 3:00 as shown in the second picture._  
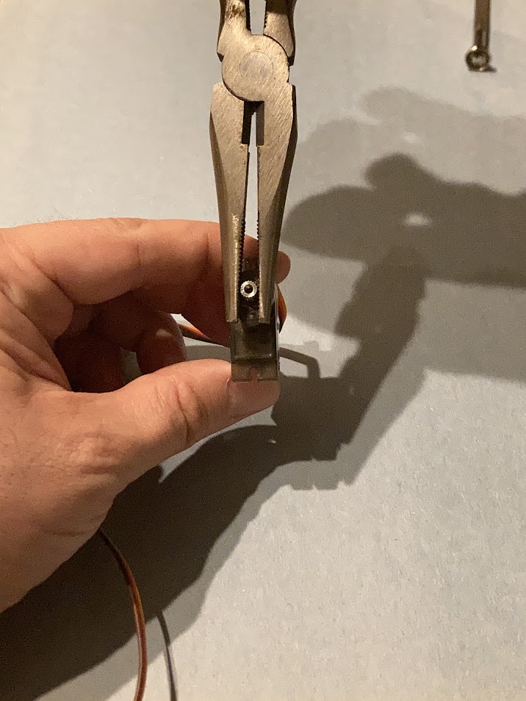
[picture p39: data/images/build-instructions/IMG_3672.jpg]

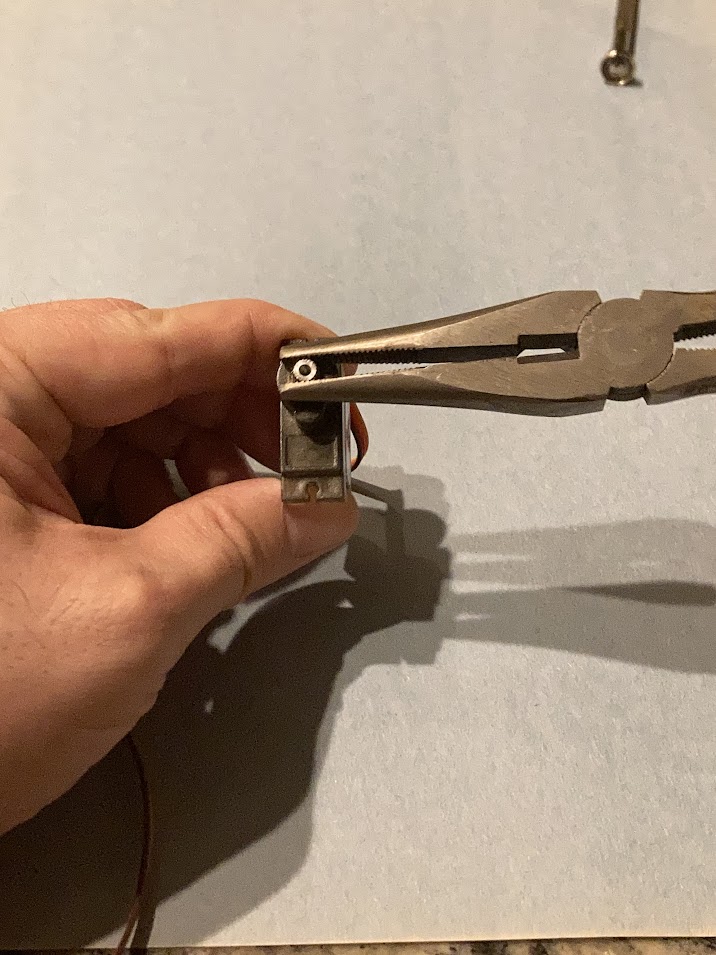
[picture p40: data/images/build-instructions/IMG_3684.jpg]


---   
### 7. Pop servo(Q) into left barrel wall(M)
**Parts:**  
   * x1 Q. MG90S 9G micro servo  
   * x2 M. left barrel wall(M) from step 5  

>_**Notes:**_
>   * _Body of servo should be on same side as fasteners from step 5_  
Head Assembly Step 5

---   
### 8. Add shaft(N) to bearing(O)
**Parts:**  
 * x1 N. head shaft adapter 
 * x1 O. bearing 

>_**Notes:**_
>   * _If shaft cannot be popped in, soften with a hair dryer or heat gun_
>   * _The longer side of the shaft should be in the bearing_
Head Assembly Step 5

---   
### 9. Attach display fasteners(K) and balance weights(L) to right barrel wall(M)
**Parts:**  
 * x1 M. head barrel wall
 * x2 K. display fastener
 * x2 P. balance weights

>_**Notes:**_
>  * _Make sure fasteners and raised center lip are on opposite sides_
Head Assembly Step 5

---   
### 10. Pop bearing(O) into right barrel wall(M)
**Parts:**  
 * x1 bearing(O) with shaft(N) from step 8
 * x1 right barrel wall(M) from step 9

>_**Notes:**_
>   * _Make sure shaft is on the opposite side of the clips & weights_
>   * _If bearing cannot be popped in, soften with a hair dryer or heat gun_
Head Assembly Step 5

---   
### 11. Attach two horizontal braces(A) with two 3-hole fasteners(B) to create lower head brace
**Parts:**  
   * x2 A. horizontal braces  
   * x2 B. 3-hole fasteners  

>_**Notes:**_
>  * _Make sure to add 3-hole fastener(B) to both sides_
Head Assembly Step 5

---   
### 12. Attach bottom head brace to left barrel wall
**Parts:**  
   * x1 Left barrel wall with servo (from step 7)  
   * x1 Lower horizontal head brace (from step 11)  
   * x2 D. 2x8mm pan-head-with-washer self-tapping screws
  
Head Assembly Step 5
Head Assembly Step 5

---   
### 13. Attach top head brace to left barrel wall
**Parts:**  
   * x1 Left barrel wall with servo (from step 12)  
   * x1 Top horizontal head brace with camera (from step 1)  
   * x2 D. 2x8mm pan-head-with-washer self-tapping screws
  
Head Assembly Step 5
Head Assembly Step 5

---   
### 14. Attach 40-pin display ribbon(S) to display(R)  
**Parts:**  
   * x1 R. 7in display  
   * x1 S. 250mm 40pin display ribbon cable  

>_**Notes:**_
>   * _Make sure pins of ribbon cable are facing toward contacts and fastened securely_
Head Assembly Step 5

---   
### 15. Pop display(S) into clips of left barrel wall(M)
**Parts:**  
   * x1 R. 7in display  
   * x1 left barrel wall with servo (from step 12)  

>_**Notes:**_
>   * _Make sure the cables are on the bottom (opposite camera) and feed bewtween both horizontal braces_

Head Assembly Step 5

---   
### 16. Pop right barrel(M) display fasteners(K) onto display and secure to horizontal braces(A) 
**Parts:**  
   * x1 right barrel wall(M) with bearing and shaft (from step 10)
   * x2 D. 2x8mm pan-head-with-washer self-tapping screws

Head Assembly Step 5

---   
### 17. Attach speaker(T)
**Parts:**  
   * x1 T. mono enclosed speaker - 3W 4 ohm
   * x2 D. 2x8mm pan-head-with-washer self-tapping screws

Head Assembly Step 5

---   
### 18. Pop right L bracket(U) on bearing shaft
**Parts:**  
   * x1 U. head L bracket

>_**Notes:**_
>   * _If shaft does not pop onto L bracket, use hair dryer or heat gun to soften_

Head Assembly Step 5

---   
### 19. Attatch servo horn to remaining L bracket(L) and secure with screw(D)
**Parts:**  
   * x1 U. head L bracket
   * x1 V. servo horn
   * x1 D. 2x8mm pan-head-with-washer self-tapping screw

Head Assembly Step 5
Head Assembly Step 5

---   
### 20. Secure left L bracket to head with servo screw(W)
**Parts:**  
   * x1 W. server screw

>_**Notes:**_
>  * _IMPORTANT: The servo horn should be pointing straight down attached with screen pointing straight left_
>  * _Be careful not to turn servo shaft when attaching. If you do, repeat step 6._

Head Assembly Step 5

---   
### 21. The head is now complete and should match the images below:  

Head Assembly Step 5
Head Assembly Step 5
Head Assembly Step 5
Head Assembly Step 5

[Return to Readme](../../README.md#table-of-contents)

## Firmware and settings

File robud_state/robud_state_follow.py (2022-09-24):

from typing import Dict
import paho.mqtt.client as mqtt
from time import sleep, monotonic
import pickle
from robud.robud_face.robud_face_common import *
import random
from robud.robud_logging.MQTTHandler import MQTTHandler
import argparse
import logging
import os
from datetime import datetime
import sys
import traceback
from robud.robud_head.robud_head_common import head_keyframe, TOPIC_HEAD_KEYFRAMES
from robud.ai.object_detection_common import TOPIC_OBJECT_DETECTION_DETECTIONS, TOPIC_OBJECT_DETECTION_REQUEST
from robud.motors.motors_common import TOPIC_HEAD_SERVO_ANGLE, TOPIC_MOTOR_LEFT_THROTTLE, TOPIC_MOTOR_RIGHT_THROTTLE
from robud.robud_voice.robud_voice_common import TOPIC_ROBUD_VOICE_TEXT_INPUT
from robud.sensors.camera_common import CAMERA_HEIGHT, CAMERA_WIDTH
from robud.sensors.tof_common import TOPIC_SENSORS_TOF_RANGE
from robud.ai.wakeword_detection.wakeword_detection_common import TOPIC_WAKEWORD_DETECTED
from robud.robud_state.robud_state_common import TOPIC_ROBUD_STATE, logger

def robud_state_follow(mqtt_client:mqtt.Client, client_userdata:Dict):
    logger.info("Starting ROBUD_STATE_FOLLOW")
    random.seed()

    HEAD_SERVO_MAX_ANGLE = 170
    HEAD_SERVO_MIN_ANGLE = 60
    SCREENHEIGHT = 320
    SCREENWIDTH = 640
    TURN_SPEED = 0.8
    MOTOR_SPEED_BASE = 0.9
    MOTOR_SPEED_ACCELERATED = 0.6
    MOTOR_SPEED_MIN = 0.2
    HEAD_ANGLE_CHANGE = 2
    HEAD_ANGLE_MAX = 180
    HEAD_ANGLE_MIN = 10
    MAX_VEERAGE = 10
    STOP_DISTANCE = 80 #centimeters or less
    BACK_UP_DISTANCE = 40

    CENTER_RANGE_WIDTH = 120

    MQTT_BROKER_ADDRESS = "robud.local"
    MQTT_CLIENT_NAME = "robud_state_follow.py" + str(random.randint(0,999999999))
    HEAD_SERVO_SPEED = 150 #degrees/sec
    PERSON_DETECTION_TIMEOUT = 50 #milliseconds
    PERSON_DETECTION_RANGE = 5000 #millimeters or less
    PERSON_DETECTION_HEIGHT = 0.67 # % of CAMERA_HEIGHT
    PERSON_DETECTION_WIDTH = 0.33 # % of CAMERA_WIDTH



    TOPIC_ROBUD_LOGGING_LOG = "robud/robud_logging/log"
    TOPIC_ROBUD_LOGGING_LOG_SIGNED = TOPIC_ROBUD_LOGGING_LOG + "/" + MQTT_CLIENT_NAME
    TOPIC_ROBUD_LOGGING_LOG_ALL = TOPIC_ROBUD_LOGGING_LOG + "/#"
    LOGGING_LEVEL = logging.DEBUG

    #SLEEP_LIGHT_LEVEL = 85
    #WAKE_LIGHT_LEVEL = 105
    MINIMUM_SLEEP = 30 #seconds
    MINIMUM_WAKE = 30 #seconds

    try:
        greetings = [
            "Okay. I'll follow you."
        ]
        
        mqtt_client.publish(TOPIC_ROBUD_VOICE_TEXT_INPUT, greetings[random.randint(0,len(greetings)-1)])
        # send a speech to text request
        
        #wait for text to finish, this should be changed to detect when audio is complete, but we'll just put a 1 second delay here.
        sleep(1)
        
        AVG_GAZE_CHANGE = 5.0 #in seconds
        AVG_EXPRESSION_CHANGE = 15.0 #in seconds

        rate = 100 #100hz rate for sending messages
        carry_on = True
        stopped=True

        object_detections = []
        client_userdata["object_detections"] = object_detections
        recognized_objects = {}
        tof_range = -1
        head_angle = None
        client_userdata["tof_range"] = tof_range
        client_userdata["head_angle"] = head_angle
        stopped=True
        target_heading = 0

        def move_forward(stopped): #,target_heading):
            left_speed = MOTOR_SPEED_BASE
            right_speed = MOTOR_SPEED_BASE
            # current_heading = int(client_userdata["heading"])
            # if stopped:
            #     target_heading = current_heading
            # elif current_heading != target_heading: 
            #     #veering to the right, add more power to right wheel
            #     veerage = abs(target_heading-current_heading)
            #     max_speed_change = MOTOR_SPEED_ACCELERATED - MOTOR_SPEED_BASE
            #     if veerage > 180: # e.g. 355 & 5
            #         veerage = abs(360-veerage)
            #         current_heading *= -1
            #         target_heading *= -1
            #     if veerage > MAX_VEERAGE:
            #         veerage_pct = 1
            #     else:
            #         veerage_pct = veerage/MAX_VEERAGE

            #     if current_heading > target_heading:              
            #         right_speed = MOTOR_SPEED_BASE + (max_speed_change * veerage_pct)
            #     elif current_heading < target_heading:
            #         #veering to the left, add more power to left wheel
            #         left_speed = MOTOR_SPEED_BASE + (max_speed_change * veerage_pct)
            # print("move forward: target_heading:{}".format(target_heading))
            stopped = False
            mqtt_client.publish(TOPIC_MOTOR_LEFT_THROTTLE, left_speed)
            mqtt_client.publish(TOPIC_MOTOR_RIGHT_THROTTLE, right_speed)
            return stopped #, target_heading

        def move_backward(stopped):
            print("move backward")
            stopped = False
            mqtt_client.publish(TOPIC_MOTOR_LEFT_THROTTLE, -1 * MOTOR_SPEED_BASE)
            mqtt_client.publish(TOPIC_MOTOR_RIGHT_THROTTLE, -1 * MOTOR_SPEED_BASE)
            return stopped
        def turn_right(stopped):
            print("turn right")
            stopped = False
            mqtt_client.publish(TOPIC_MOTOR_LEFT_THROTTLE, TURN_SPEED)
            mqtt_client.publish(TOPIC_MOTOR_RIGHT_THROTTLE, -1 * TURN_SPEED)
            return stopped
        def turn_left(stopped):
            print("turn left")
            stopped = False
            mqtt_client.publish(TOPIC_MOTOR_LEFT_THROTTLE, -1 * TURN_SPEED)
            mqtt_client.publish(TOPIC_MOTOR_RIGHT_THROTTLE, TURN_SPEED)
            return stopped
        def stop(stopped):
            print("stop", target_heading)
            stopped = True
            mqtt_client.publish(TOPIC_MOTOR_LEFT_THROTTLE, 0)
            mqtt_client.publish(TOPIC_MOTOR_RIGHT_THROTTLE, 0)
            return stopped
        def look_up(head_angle):
            print("look up")
            new_angle = head_angle + HEAD_ANGLE_CHANGE
            if new_angle >= HEAD_ANGLE_MAX: 
                new_angle = HEAD_ANGLE_MAX
            head_angle = new_angle
            mqtt_client.publish(TOPIC_HEAD_SERVO_ANGLE, head_angle,retain=True)
            return head_angle

        def look_down(head_angle):
            print("look down")
            new_angle = head_angle - HEAD_ANGLE_CHANGE
            if new_angle <= HEAD_ANGLE_MIN:
                new_angle = HEAD_ANGLE_MIN 
            head_angle = new_angle
            mqtt_client.publish(TOPIC_HEAD_SERVO_ANGLE, head_angle,retain=True)
            return head_angle

        def move_eyes(
            face_expression, 
            left_expression:ExpressionCoordinates, 
            right_expression:ExpressionCoordinates, 
            selected_position:tuple,
            change_expression:bool,
            head_angle:int,
            new_head_angle:int,
            mqtt_client:mqtt.Client,
            duration:float = EXPRESSION_CHANGE_DURATION,
            head_duration:float = None):    
            if (
                change_expression
                or
                face_expression[CENTER_X_OFFSET] != selected_position[0]
                or 
                face_expression[CENTER_Y_OFFSET] != selected_position[1]
                ):
                face_expression[CENTER_X_OFFSET] = selected_position[0]
                face_expression[CENTER_Y_OFFSET] = selected_position[1]
                new_face_keyframe = face_keyframe(
                    left_expression=left_expression,
                    right_expression=right_expression,
                    position=selected_position,
                    duration=duration
                )

                if head_duration == None:
                    #figure out head duration based on HEAD_SERVO_SPEED
                    head_duration = abs(new_head_angle - head_angle) * (1/HEAD_SERVO_SPEED)
                
                new_head_keyframe = head_keyframe(
                    angle = new_head_angle,
                    duration=head_duration
                )

                #add the keyframes to lists
                face_keyframes = [new_face_keyframe]
                head_keyframes = [new_head_keyframe]


                #publish them!
                mqtt_client.publish(TOPIC_FACE_KEYFRAMES,pickle.dumps(face_keyframes),qos=2)
                mqtt_client.publish(TOPIC_HEAD_KEYFRAMES,pickle.dumps(head_keyframes),qos=2)
                change_expression = False
            return face_expression, change_expression, new_head_angle

        def on_message_object_detections(client, userdata, message):
            userdata["object_detections"] = pickle.loads(message.payload)

        def on_message_tof_range(client, userdata, message):
            userdata["tof_range"] = int(message.payload)

        def on_message_head_angle(client, userdata, message):
            userdata["head_angle"] = int(message.payload)

        def on_message_wakeword_detected(client:mqtt.Client, userdata,message):
             client.publish(TOPIC_ROBUD_STATE, "ROBUD_STATE_WAKEWORD_DETECTED")


        mqtt_client.subscribe(TOPIC_OBJECT_DETECTION_DETECTIONS)
        mqtt_client.message_callback_add(TOPIC_OBJECT_DETECTION_DETECTIONS,on_message_object_detections)
        logger.info('Subcribed to ' + TOPIC_OBJECT_DETECTION_DETECTIONS)
        mqtt_client.subscribe(TOPIC_SENSORS_TOF_RANGE)
        mqtt_client.message_callback_add(TOPIC_SENSORS_TOF_RANGE,on_message_tof_range)
        logger.info('Subcribed to ' + TOPIC_SENSORS_TOF_RANGE)
        mqtt_client.subscribe(TOPIC_HEAD_SERVO_ANGLE)
        mqtt_client.message_callback_add(TOPIC_HEAD_SERVO_ANGLE,on_message_head_angle)
        logger.info('Subcribed to ' + TOPIC_HEAD_SERVO_ANGLE)
        mqtt_client.subscribe(TOPIC_WAKEWORD_DETECTED)
        mqtt_client.message_callback_add(TOPIC_WAKEWORD_DETECTED,on_message_wakeword_detected)
        logger.info('Subcribed to ' + TOPIC_WAKEWORD_DETECTED)

        #init face expression
        face_expression = np.zeros(shape=FACE_EXPRESSION_ARRAY_SIZE, dtype=np.int16)
        set_expression(face_expression, Expressions[ExpressionId.OPEN])
        selected_expression = Expressions[ExpressionId.OPEN]
        left_expression:ExpressionCoordinates = Expressions[ExpressionId.OPEN]
        right_expression:ExpressionCoordinates = Expressions[ExpressionId.OPEN]
        position_left = 50
        position_right = -50
        position_center = 0
        position_up = -50
        position_down = 50
        position_sleep = 100
        angle_center = 90
        selected_position = (position_center,position_center)
        change_expression:bool = False
        last_dog_detection = 0
        #tof_range = -1
        sleeping = False
        wake_time = monotonic()
        sleep_time = 0
        #start by looking up at 135 degree angle
        gaze_vertical = position_up
        new_head_angle = 150
        gaze_horizontal = position_center
        last_person_detection = 0
        while client_userdata["published_state"] == "ROBUD_STATE_FOLLOW":
            loop_start = monotonic()
            duration = EXPRESSION_CHANGE_DURATION
            head_duration = 0
            tof_range = client_userdata["tof_range"]
            head_angle = client_userdata["head_angle"]
            
            selected_position = (gaze_horizontal,gaze_vertical)
            change_expression = True
            
            if loop_start - last_person_detection > PERSON_DETECTION_TIMEOUT:
                #look for a person to follow
                client_userdata["object_detections"] = None
                mqtt_client.publish(topic=TOPIC_OBJECT_DETECTION_REQUEST,payload=int(True))    
                logger.info("object detection requested")
                logger.info("waiting for object detection response...")
                start_wait = monotonic()
                while (
                    client_userdata["object_detections"] is None
                    and monotonic() - start_wait < 1
                ):
                    sleep(0.01)
                if client_userdata["object_detections"] is None:
                    logger.info("object detection timeout")
                    last_person_detection = monotonic()
                else:
                    logger.info("object detection response receieved")
                
            if client_userdata["object_detections"] is not None:
                for detection in client_userdata["object_detections"]:               
                    if (
                        detection["ClassLabel"] == "person" 
                        ):
                        logging.debug("PERSON DETECTED")
                        
                        # check if person is centered
                        person_horizontal_center = detection["Center"][0]
                        center_range_low = CAMERA_WIDTH/2 - CENTER_RANGE_WIDTH/2
                        center_range_high = CAMERA_WIDTH/2 + CENTER_RANGE_WIDTH/2

                        if person_horizontal_center < center_range_low:
                            #person to left
                            logging.debug("person detected to left")
                            turn_left("stopped")
                        elif person_horizontal_center > center_range_high:
                            #person to right
                            logging.debug("person detected to right")
                            turn_right("stopped")
                        else:
                            #person centered!
                            logging.debug("person centered!")
                            if tof_range > STOP_DISTANCE:
                                move_forward(stopped)
                            elif tof_range < BACK_UP_DISTANCE:
                                move_backward(stopped)



            face_expression, change_expression, new_head_angle = move_eyes(
                    face_expression = face_expression,
                    left_expression = left_expression,
                    right_expression = right_expression,
                    selected_position = selected_position,
                    change_expression = change_expression,
                    mqtt_client = mqtt_client,
                    head_angle = head_angle,
                    new_head_angle=new_head_angle,
                    duration=duration,
                    head_duration=head_duration
                    )

            loop_time = monotonic() - loop_start
            if loop_time < 1/rate:
                sleep(1/rate - loop_time)
        #transition out of state & clean up
        logger.info("State change detected:" + client_userdata["published_state"])
        #unsubscribe from all 
        logger.info("Finishing up of ROBUD_STATE_FOLLOW")
        mqtt_client.unsubscribe(TOPIC_OBJECT_DETECTION_DETECTIONS)
        logger.info("Unsubscribed from " + TOPIC_OBJECT_DETECTION_DETECTIONS)
        mqtt_client.unsubscribe(TOPIC_SENSORS_TOF_RANGE)
        logger.info("Unsubscribed from " + TOPIC_SENSORS_TOF_RANGE)
        mqtt_client.unsubscribe(TOPIC_HEAD_SERVO_ANGLE)
        logger.info("Unsubscribed from " + TOPIC_HEAD_SERVO_ANGLE)
        mqtt_client.unsubscribe(TOPIC_WAKEWORD_DETECTED)
        logger.info('Unsubscribed from' + TOPIC_WAKEWORD_DETECTED)
        logger.info("Exiting ROBUD_STATE_FOLLOW")
    except Exception as e:
        logger.critical(str(e) + "\n" + traceback.format_exc())              

if __name__ == "__main__":
    MQTT_BROKER_ADDRESS = "robud.local"
    MQTT_CLIENT_NAME = "robud_state_follow.py" + str(random.randint(0,999999999))
    client_userdata = {}
    mqtt_client = mqtt.Client(client_id=MQTT_CLIENT_NAME, userdata=client_userdata)
    mqtt_client.connect(MQTT_BROKER_ADDRESS)
    mqtt_client.loop_start()
    logger.info('MQTT Client Connected')
    def on_message_robud_state(client, userdata, message):
        userdata["published_state"] = message.payload.decode()
    client_userdata["published_state"] = "ROBUD_STATE_FOLLOW"
    mqtt_client.subscribe(TOPIC_ROBUD_STATE)
    mqtt_client.message_callback_add(TOPIC_ROBUD_STATE,on_message_robud_state)
    logger.info('Subcribed to ' + TOPIC_ROBUD_STATE)
    mqtt_client.publish(topic=TOPIC_ROBUD_STATE, payload = "ROBUD_STATE_FOLLOW", retain=True)
    robud_state_follow(mqtt_client, client_userdata)

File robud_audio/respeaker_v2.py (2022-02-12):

# copied from https://github.com/respeaker/usb_4_mic_array/blob/master/tuning.py
# -*- coding: utf-8 -*-

import sys
import struct
import usb.core
import usb.util

USAGE = """Usage: python {} -h
        -p      show all parameters
        -r      read all parameters
        NAME    get the parameter with the NAME
        NAME VALUE  set the parameter with the NAME and the VALUE
"""



# parameter list
# name: (id, offset, type, max, min , r/w, info)
PARAMETERS = {
    'AECFREEZEONOFF': (18, 7, 'int', 1, 0, 'rw', 'Adaptive Echo Canceler updates inhibit.', '0 = Adaptation enabled', '1 = Freeze adaptation, filter only'),
    'AECNORM': (18, 19, 'float', 16, 0.25, 'rw', 'Limit on norm of AEC filter coefficients'),
    'AECPATHCHANGE': (18, 25, 'int', 1, 0, 'ro', 'AEC Path Change Detection.', '0 = false (no path change detected)', '1 = true (path change detected)'),
    'RT60': (18, 26, 'float', 0.9, 0.25, 'ro', 'Current RT60 estimate in seconds'),
    'HPFONOFF': (18, 27, 'int', 3, 0, 'rw', 'High-pass Filter on microphone signals.', '0 = OFF', '1 = ON - 70 Hz cut-off', '2 = ON - 125 Hz cut-off', '3 = ON - 180 Hz cut-off'),
    'RT60ONOFF': (18, 28, 'int', 1, 0, 'rw', 'RT60 Estimation for AES. 0 = OFF 1 = ON'),
    'AECSILENCELEVEL': (18, 30, 'float', 1, 1e-09, 'rw', 'Threshold for signal detection in AEC [-inf .. 0] dBov (Default: -80dBov = 10log10(1x10-8))'),
    'AECSILENCEMODE': (18, 31, 'int', 1, 0, 'ro', 'AEC far-end silence detection status. ', '0 = false (signal detected) ', '1 = true (silence detected)'),
    'AGCONOFF': (19, 0, 'int', 1, 0, 'rw', 'Automatic Gain Control. ', '0 = OFF ', '1 = ON'),
    'AGCMAXGAIN': (19, 1, 'float', 1000, 1, 'rw', 'Maximum AGC gain factor. ', '[0 .. 60] dB (default 30dB = 20log10(31.6))'),
    'AGCDESIREDLEVEL': (19, 2, 'float', 0.99, 1e-08, 'rw', 'Target power level of the output signal. ', '[-inf .. 0] dBov (default: -23dBov = 10log10(0.005))'),
    'AGCGAIN': (19, 3, 'float', 1000, 1, 'rw', 'Current AGC gain factor. ', '[0 .. 60] dB (default: 0.0dB = 20log10(1.0))'),
    'AGCTIME': (19, 4, 'float', 1, 0.1, 'rw', 'Ramps-up / down time-constant in seconds.'),
    'CNIONOFF': (19, 5, 'int', 1, 0, 'rw', 'Comfort Noise Insertion.', '0 = OFF', '1 = ON'),
    'FREEZEONOFF': (19, 6, 'int', 1, 0, 'rw', 'Adaptive beamformer updates.', '0 = Adaptation enabled', '1 = Freeze adaptation, filter only'),
    'STATNOISEONOFF': (19, 8, 'int', 1, 0, 'rw', 'Stationary noise suppression.', '0 = OFF', '1 = ON'),
    'GAMMA_NS': (19, 9, 'float', 3, 0, 'rw', 'Over-subtraction factor of stationary noise. min .. max attenuation'),
    'MIN_NS': (19, 10, 'float', 1, 0, 'rw', 'Gain-floor for stationary noise suppression.', '[-inf .. 0] dB (default: -16dB = 20log10(0.15))'),
    'NONSTATNOISEONOFF': (19, 11, 'int', 1, 0, 'rw', 'Non-stationary noise suppression.', '0 = OFF', '1 = ON'),
    'GAMMA_NN': (19, 12, 'float', 3, 0, 'rw', 'Over-subtraction factor of non- stationary noise. min .. max attenuation'),
    'MIN_NN': (19, 13, 'float', 1, 0, 'rw', 'Gain-floor for non-stationary noise suppression.', '[-inf .. 0] dB (default: -10dB = 20log10(0.3))'),
    'ECHOONOFF': (19, 14, 'int', 1, 0, 'rw', 'Echo suppression.', '0 = OFF', '1 = ON'),
    'GAMMA_E': (19, 15, 'float', 3, 0, 'rw', 'Over-subtraction factor of echo (direct and early components). min .. max attenuation'),
    'GAMMA_ETAIL': (19, 16, 'float', 3, 0, 'rw', 'Over-subtraction factor of echo (tail components). min .. max attenuation'),
    'GAMMA_ENL': (19, 17, 'float', 5, 0, 'rw', 'Over-subtraction factor of non-linear echo. min .. max attenuation'),
    'NLATTENONOFF': (19, 18, 'int', 1, 0, 'rw', 'Non-Linear echo attenuation.', '0 = OFF', '1 = ON'),
    'NLAEC_MODE': (19, 20, 'int', 2, 0, 'rw', 'Non-Linear AEC training mode.', '0 = OFF', '1 = ON - phase 1', '2 = ON - phase 2'),
    'SPEECHDETECTED': (19, 22, 'int', 1, 0, 'ro', 'Speech detection status.', '0 = false (no speech detected)', '1 = true (speech detected)'),
    'FSBUPDATED': (19, 23, 'int', 1, 0, 'ro', 'FSB Update Decision.', '0 = false (FSB was not updated)', '1 = true (FSB was updated)'),
    'FSBPATHCHANGE': (19, 24, 'int', 1, 0, 'ro', 'FSB Path Change Detection.', '0 = false (no path change detected)', '1 = true (path change detected)'),
    'TRANSIENTONOFF': (19, 29, 'int', 1, 0, 'rw', 'Transient echo suppression.', '0 = OFF', '1 = ON'),
    'VOICEACTIVITY': (19, 32, 'int', 1, 0, 'ro', 'VAD voice activity status.', '0 = false (no voice activity)', '1 = true (voice activity)'),
    'STATNOISEONOFF_SR': (19, 33, 'int', 1, 0, 'rw', 'Stationary noise suppression for ASR.', '0 = OFF', '1 = ON'),
    'NONSTATNOISEONOFF_SR': (19, 34, 'int', 1, 0, 'rw', 'Non-stationary noise suppression for ASR.', '0 = OFF', '1 = ON'),
    'GAMMA_NS_SR': (19, 35, 'float', 3, 0, 'rw', 'Over-subtraction factor of stationary noise for ASR. ', '[0.0 .. 3.0] (default: 1.0)'),
    'GAMMA_NN_SR': (19, 36, 'float', 3, 0, 'rw', 'Over-subtraction factor of non-stationary noise for ASR. ', '[0.0 .. 3.0] (default: 1.1)'),
    'MIN_NS_SR': (19, 37, 'float', 1, 0, 'rw', 'Gain-floor for stationary noise suppression for ASR.', '[-inf .. 0] dB (default: -16dB = 20log10(0.15))'),
    'MIN_NN_SR': (19, 38, 'float', 1, 0, 'rw', 'Gain-floor for non-stationary noise suppression for ASR.', '[-inf .. 0] dB (default: -10dB = 20log10(0.3))'),
    'GAMMAVAD_SR': (19, 39, 'float', 1000, 0, 'rw', 'Set the threshold for voice activity detection.', '[-inf .. 60] dB (default: 3.5dB 20log10(1.5))'),
    # 'KEYWORDDETECT': (20, 0, 'int', 1, 0, 'ro', 'Keyword detected. Current value so needs polling.'),
    'DOAANGLE': (21, 0, 'int', 359, 0, 'ro', 'DOA angle. Current value. Orientation depends on build configuration.')
}
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

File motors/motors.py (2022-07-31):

from math import e
from time import sleep, time
from adafruit_motorkit import MotorKit
from adafruit_servokit import ServoKit
from adafruit_motor import servo
import paho.mqtt.client as mqtt
from robud.robud_logging.MQTTHandler import MQTTHandler
import logging
import random
import argparse
from datetime import datetime
import os
import traceback
import sys

import board

random.seed()

MOTOR_TIMEOUT = 0.2
MQTT_BROKER_ADDRESS = "robud.local"
MQTT_CLIENT_NAME = "robud_motors_motors.py" + str(random.randint(0,999999999))
TOPIC_MOTOR_LEFT_THROTTLE = 'robud/motors/motor_left/throttle'
TOPIC_MOTOR_RIGHT_THROTTLE = 'robud/motors/motor_right/throttle'
TOPIC_HEAD_SERVO_ANGLE = 'robud/motors/head_servo/angle'
HEAD_SERVO_MAX_ANGLE = 180
HEAD_SERVO_MIN_ANGLE = 0

TOPIC_ROBUD_LOGGING_LOG = "robud/robud_logging/log"
TOPIC_ROBUD_LOGGING_LOG_SIGNED = TOPIC_ROBUD_LOGGING_LOG + "/" + MQTT_CLIENT_NAME
TOPIC_ROBUD_LOGGING_LOG_ALL = TOPIC_ROBUD_LOGGING_LOG + "/#"
LOGGING_LEVEL= logging.DEBUG

#parse arguments
parser = argparse.ArgumentParser()
parser.add_argument("-o", "--Output", help="Log Ouput Prefix", default="logs/motors_log_")
args = parser.parse_args()

#initialize logger
logger=logging.getLogger()
file_path = args.Output + datetime.now().strftime("%Y-%m-%d") + ".txt"
directory = os.path.dirname(file_path)
if not os.path.exists(directory):
    os.makedirs(directory)
log_file = open(file_path, "a")
myHandler = MQTTHandler(hostname=MQTT_BROKER_ADDRESS, topic=TOPIC_ROBUD_LOGGING_LOG_SIGNED, qos=2, log_file=log_file)
myHandler.setFormatter(logging.Formatter('%(asctime)s - %(levelname)s: %(filename)s: %(message)s'))
logger.addHandler(myHandler)
logger.level = LOGGING_LEVEL

try:
    logger.info("Intializing")

    class RobudMotorWapper(object):
        def __init__(self,motor,motor_name) -> None:
            super().__init__()
            self.motor = motor
            self.timeout_start = 0
            self.name = motor_name
        
        def stopIfTimeout(self):
            if self.timeout_start != 0 and time() - self.timeout_start > MOTOR_TIMEOUT:
                logger.debug("motor timeout:" +  self.name)
                self.motor.throttle = 0
                self.timeout_start = 0 

    def on_message_motor_throttle(client, userdata, message):
        print(message.topic, message.payload)
        robud_motor = None
        if message.topic == TOPIC_MOTOR_LEFT_THROTTLE:
            robud_motor = userdata["motor_left"]
        elif message.topic == TOPIC_MOTOR_RIGHT_THROTTLE:
            robud_motor = userdata["motor_right"]
        else:
            raise ValueError('Invalid Topic: {}'.format(message.topic))
        try:
            #convert message payload to float
            throttle = float(message.payload)
            #make sure throttle is between -1 and 1
            if throttle < -1 or throttle > 1:
                raise ValueError
            #finally set throttle!
            robud_motor.motor.throttle = throttle
            robud_motor.timeout_start = time()
        except ValueError:
            raise ValueError('Invalid Throttle Value: {}'.format(message.payload))
            
    def on_message_servo_angle(client, userdata, message):
        print(message.topic, message.payload)
        head_servo = userdata["head_servo"]
        try:
            #convert message payload to int
            angle = int(message.payload)
            if angle < HEAD_SERVO_MIN_ANGLE or angle > HEAD_SERVO_MAX_ANGLE:
                raise ValueError
            head_servo.angle = angle
        except ValueError:
            raise ValueError('Invalid Servo Angle: {}'.format(message.payload))



    kit = MotorKit() #need frequency of 50hz for servo
    servokit = ServoKit(channels=16, address = 0x41)
    head_servo = servokit.servo[15]
    #kit = None
    motor_right = RobudMotorWapper(kit.motor1, "motor_right")
    motor_left = RobudMotorWapper(kit.motor2, "motor_left")
    #add anything that needs to be handled by mqtt callbacks to 
    #client_userdata, and pass that into the client
    client_userdata = {
        "head_servo":head_servo,
        "motor_left":motor_left,
        "motor_right":motor_right
    }
    mqtt_client = mqtt.Client(client_id=MQTT_CLIENT_NAME,userdata=client_userdata)
    mqtt_client.connect(MQTT_BROKER_ADDRESS)
    mqtt_client.loop_start()
    logger.info('MQTT Client Connected')
    mqtt_client.subscribe(TOPIC_MOTOR_LEFT_THROTTLE)
    mqtt_client.message_callback_add(TOPIC_MOTOR_LEFT_THROTTLE,on_message_motor_throttle)
    logger.info('Subcribed to ' + TOPIC_MOTOR_LEFT_THROTTLE)
    mqtt_client.subscribe(TOPIC_MOTOR_RIGHT_THROTTLE)
    mqtt_client.message_callback_add(TOPIC_MOTOR_RIGHT_THROTTLE,on_message_motor_throttle)
    logger.info('Subcribed to ' + TOPIC_MOTOR_RIGHT_THROTTLE)
    mqtt_client.subscribe(TOPIC_HEAD_SERVO_ANGLE)
    mqtt_client.message_callback_add(TOPIC_HEAD_SERVO_ANGLE,on_message_servo_angle)
    logger.info('Subcribed to' + TOPIC_HEAD_SERVO_ANGLE)
    logger.info('Waiting for messages...')

    #main loop:
    while True:
        #stop the motors if they haven't received a message for the length of the timeout
        motor_left.stopIfTimeout()
        motor_right.stopIfTimeout()
        sleep(0.01)
except Exception as e:
    logger.critical(str(e) + "\n" + traceback.format_exc())
except KeyboardInterrupt:
    logger.info("Exited with Keyboard Interrupt")
    try:
        sys.exit(0)
    except SystemExit:
        os._exit(0)

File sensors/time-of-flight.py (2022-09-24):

import board
import busio
import adafruit_vl53l0x
import time
import statistics
import paho.mqtt.client as mqtt
import random
from robud.robud_logging.MQTTHandler import MQTTHandler
import argparse
import logging
from datetime import datetime
import os
import sys
import traceback
from robud.sensors.tof_common import TOPIC_SENSORS_TOF_RANGE

random.seed()

MQTT_BROKER_ADDRESS = "robud.local"
MQTT_CLIENT_NAME = "time-of-flight.py" + str(random.randint(0,999999999))

TOPIC_ROBUD_LOGGING_LOG = "robud/robud_logging/log"
TOPIC_ROBUD_LOGGING_LOG_SIGNED = TOPIC_ROBUD_LOGGING_LOG + "/" + MQTT_CLIENT_NAME
TOPIC_ROBUD_LOGGING_LOG_ALL = TOPIC_ROBUD_LOGGING_LOG + "/#"
LOGGING_LEVEL = logging.DEBUG

#parse arguments
parser = argparse.ArgumentParser()
parser.add_argument("-o", "--Output", help="Log Ouput Prefix", default="logs/time-of-flight_log_")
args = parser.parse_args()

#initialize logger
logger=logging.getLogger()
file_path = args.Output + datetime.now().strftime("%Y-%m-%d") + ".txt"
directory = os.path.dirname(file_path)
if not os.path.exists(directory):
    os.makedirs(directory)
log_file = open(file_path, "a")
myHandler = MQTTHandler(hostname=MQTT_BROKER_ADDRESS, topic=TOPIC_ROBUD_LOGGING_LOG_SIGNED, qos=2, log_file=log_file)
myHandler.setFormatter(logging.Formatter('%(asctime)s - %(levelname)s: %(filename)s: %(message)s'))
logger.addHandler(myHandler)
logger.level = LOGGING_LEVEL

try:
    logger.info("starting")
    i2c = busio.I2C(board.SCL, board.SDA)
    sensor = adafruit_vl53l0x.VL53L0X(i2c)
    sample_size = 4
    tolerance = 0.05
    rate = 5 #publish rate in hz
    topic = TOPIC_SENSORS_TOF_RANGE

    def get_range_from_sample(sample):
        #first get median from sample
        median = statistics.median(sample)
        #now check if all values are in tolerance
        for measurement in sample:
            if abs(median - measurement) > tolerance * median:
                return -1
        return int(sum(sample)/len(sample)/10)

    client = mqtt.Client(MQTT_CLIENT_NAME) #create new instance
    client.connect(MQTT_BROKER_ADDRESS)
    #to make this useful, we'll only publish if the sample set are within tolerance of each other
    client.loop_start()
    while True:
        try:
            loop_start = time.time()
            sample = []
            for i in range(sample_size-1):
                sample.append(sensor.range)
            tof_range = get_range_from_sample(sample)
            #logger.debug('{} cm'.format(tof_range))
            if tof_range > -1:
                client.publish(topic=topic,payload=tof_range,qos=2)
            loop_time = time.time()-loop_start
            if (loop_time<1/rate):
                time.sleep( 1/rate - loop_time)
        except OSError as e:
            logger.error(str(e) + "\n" + traceback.format_exc())
except Exception as e:
    logger.critical(str(e) + "\n" + traceback.format_exc())
except KeyboardInterrupt:
    logger.info("Exited with Keyboard Interrupt")
finally:    
    exit(0)


  
    

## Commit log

2021-06-27 Updates for Jetson Nano
2021-06-27 Moved motors folder to root
2021-06-28 Updated Keyboard Controller. Moved Camera moniter to utils.
2021-06-29 updated motors & camera. Started image segmentation.
2021-07-20 Update Keyboard controller for head servo
2021-07-31 Clean up, optimized as systemd services, fixed eye direction
    [camera.py, keyboard_controller.py, orientation.py]
2021-08-01 Added left and right wheel odometry
2021-08-27 Added mouse odometry
2021-08-27 Updated pid function for wheels to account for veerage over 180 degrees (e.g. 355 & 5)
2021-09-25 Added logging to motors.pyy
2021-10-03 Added base-build images, competed soldering documentation
2021-10-03 Added STLs
    [robud-1-hole-fastener.stl, robud-3-hole-fastener.stl, robud-display-fastener.stl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]
2021-10-03 Added first stl link to readme.md. Need to test live on github.
2021-10-03 STL link fixes
2021-10-06 Created separate head-assembly.md
2021-11-27 Added head servo to key frames
2021-11-27 Logged motor timeout
2021-11-27 Removed head servo from keyframes - was causing more problems than good.
    [keyboard_controller.py]
2021-11-29 added more greetings and reduced object detection rate to 5hz
2021-11-29 Added additional error handling to time-of-flight to prevent crash
    [time-of-flight.py]
2021-11-29 Fixed error logging mistake that prevented Ctrl-C
    [time-of-flight.py]
2021-11-30 Added light_level sensor
2021-11-30 Camera Exposure Mode didn't work. Removing.
    [camera.py]
2021-12-03 Modify object detection to only process on request for performance and power savings
2021-12-03 Added camera raw callback
2022-02-23 Removed output stream because of crashes.
    [robud_audio.py]
2022-08-17 Update README.md
    Updating head-assembly.
    Removing out-of-date instructions.
2022-08-17 Update README.md
    Re-organizing parts list for head-assembly
2022-08-17 Update README.md
    Replaced manual servo back-drive with servo tester
2022-08-17 Update README.md
    Added heat shrink tubing to parts list
2022-08-17 Update README.md
    Removed unneeded display extension cable.
2022-09-13 stick and ultrasonics
2022-09-18 Added ultrasonics service
